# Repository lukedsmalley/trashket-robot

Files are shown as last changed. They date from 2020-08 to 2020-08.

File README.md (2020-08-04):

<div align="center">
  <h1>Trashket Robot</h1>
  <h3>Trash-catching mobile wastebasket</h3>
  <h4>Term project for GSU's Embedded Systems course in the spring of 2020 by Luke Smalley, Byron Mouen, and Christian Moronta</h4>
</div>
  
The course instructor was [Doctor Michael Weeks](https://hallertau.cs.gsu.edu/~mweeks/index.html), who maintains [this webpage](https://hallertau.cs.gsu.edu/~mweeks/csc4110/) for the course in current and past terms (Those links are active as this document is written, but is apparently running on some box inside the GSU CS department, so may not be available forever).

The statement submitted for the project abstract/goal was the following:
> Trashketball is the game that every ambitious person with a wad of trash will probably engage in. One plays trashketball using a wad of trash and a trash basket (trashket). A game of trashket ball consists of one or more attempts to toss one's trash into the basket from any distance. One wins at trashketball by throwing the trash such that it lands inside the trashket.
The goal of this project is to create a trashket that moves by itself so that it will catch any trash thrown at it with as much success as possible. To accomplish this, we must construct a mobile robotic system with the capability to track thrown objects. This requires a wastebasket be assembled with a number of other distinct subsystems:<br>- A mobility subsystem that can change direction and move quickly<br>- A vision subsystem to track thrown trash<br>- A subsystem to detect caught trash and keep score (optionally)

Prior art research yielded only the mobile trash can developed by Japanese engineer Minoru Kurata (See Kurata's [development and home demo video](https://www.youtube.com/watch?v=NqDTE6dHpJw) and [expo demo](https://www.youtube.com/watch?v=ZNWd4FFYDv0)). Kurata's trash can uses an elaborate custom-fabricated driving base that allows it to change its direction of travel without rotating the chassis or wastebasket. Thrown trash was tracked using a wall-mounted Microsoft Kinect. Duplicating the mobility system of this device was well beyond our fabrication capabilities. Based on this research, we knew we could either approach object tracking using a stationary camera or a camera mounted to the mobile assembly.

### Initial Prototype

We had plenty of hobby microcontrollers and cameras available between ourselves, but no suitable sets of compatible chassis parts and motors. Since suitably-powerful motors are expensive in the context of a college course, we designed the driving base using the minimum number of motors necessary. A two-wheel, two-motor driving base would minimize the cost of parts, albeit sacrificing our ability to turn quickly. We prepared to buy the lowest-cost motors, but a friend lent us a pair of [VEX 393 motors](https://www.vexrobotics.com/motors.html), along with the 7.2V batteries used by the VEX system.

LEGO Technic parts were the most readily accessible material for a chassis, but the VEX motors needed to be attached to the LEGO beams, gearing, and wheels. Because we had access to a 3D printer, we designed and printed components to connect VEX motors and axle to Technic parts.

<div align="center">
  <p><i>Renders of the VEX-LEGO axle coupler and motor mount bracket</i></p>
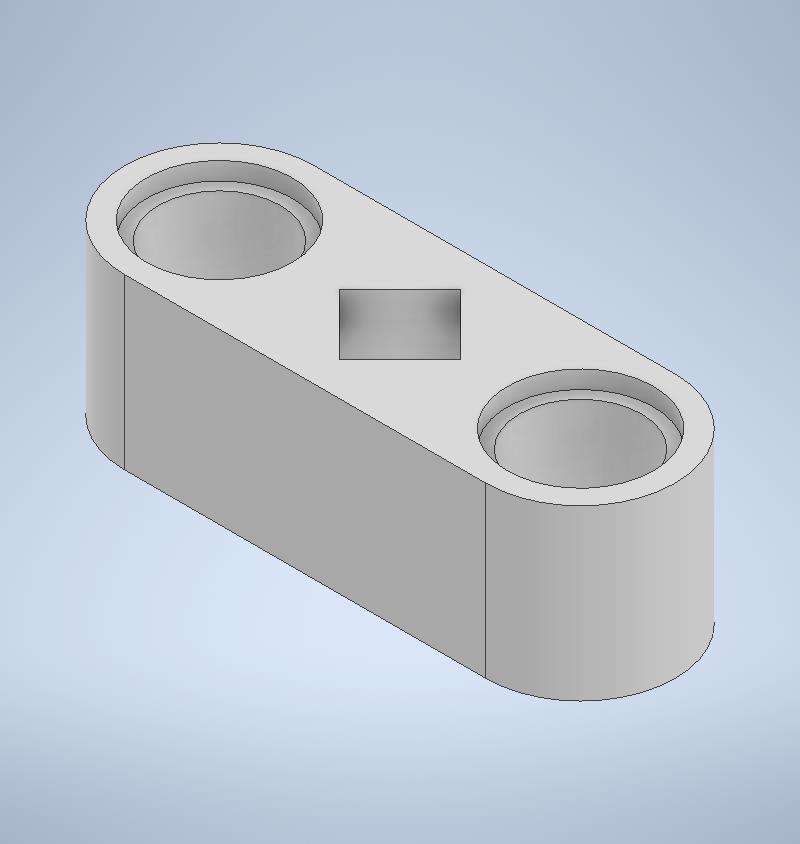
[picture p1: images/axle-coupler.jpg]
Render of the VEX-LEGO axle coupler
  
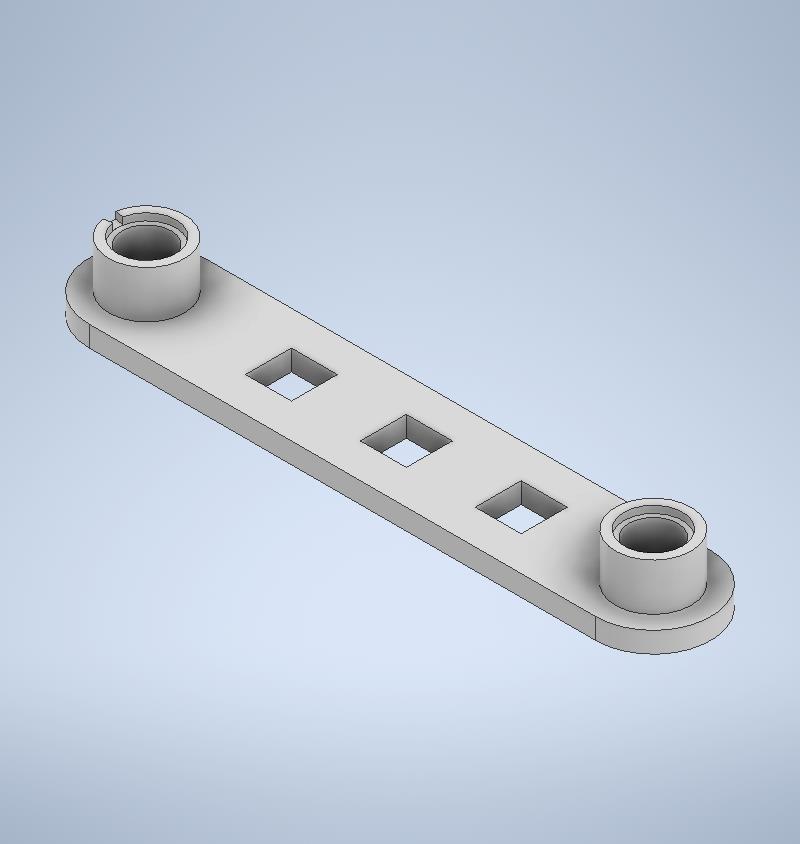
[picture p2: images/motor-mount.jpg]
Render of the VEX-LEGO motor-mounting bracket
  
  <p><i>VEX motors with 1/8" axle mounted and interfaced with the final LEGO chassis</i></p>
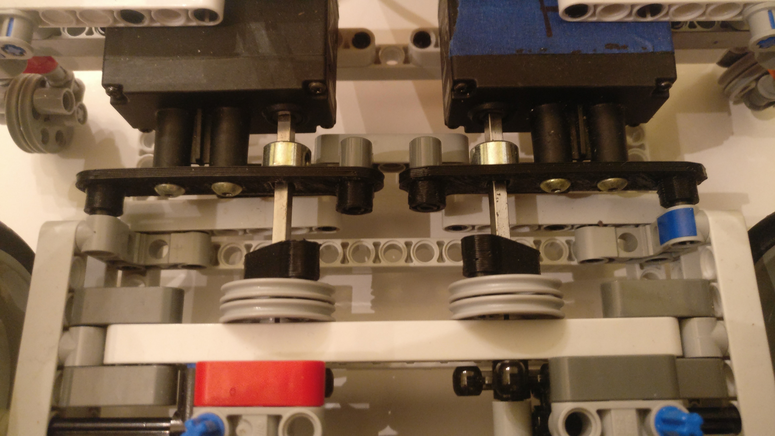
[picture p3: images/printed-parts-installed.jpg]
Photo of the VEX motors mounted tot he LEGO chassis
  
</div>

An initial prototype served as proof-of-concept for the circuitry, though it was not complex. The chassis was constructed to carry the minimum necessary electronics, but not a full-sized trash can. This first assembly was also a test of strength for the chassis and gearing, to see if the LEGO parts could support the torque of the VEX motors. The prototype only used two MOSFETs to control the motors, and could only drive forward. The electronics configuration of the first prototype was as follows:

```
    +--------------+                 +--------+     +------------+
    | 7.2V Battery | -----------.--> | MOSFET | --> | Left Motor |
    +--------------+            |    +--------+     +------------+
           |                    v         ^ 
           v                 +--------+   |    +-------------+
+-----------------------+    | MOSFET | --:--> | Right Motor |
| 6-12V to 5V Converter |    +--------+   |    +-------------+
+-----------------------+         ^       |
           |                      |       |
           v                      |       |
   +-----------------+            |       |
   | Raspberry Pi 3B | -----------'-------' 
   +-----------------+
```

<div align="center">
  <p><i>Wonderful photo of the first prototype</i></p>
  Photo of the first prototype
</div>

A worthwhile note about the photo above: the black PCBs slotted into the breadboard are the MOSFETs which regulate motor speed. The boards include a transistor and opto-isolator between the control pin and MOSFET base. Unnecessary as that may be, I already had several around. Additionally, I'm not an electrical engineer.

We used a very simple Python program, running on the Raspberry Pi depicted above, to verify that the robot functioned:

```python
# trashket-robot/scripts/circle.py

from gpiozero import PWMLED
from time import sleep

left = PWMLED(17)
right = PWMLED(22)

try:
  left.value = 0.1
  while True:
    right.value = 0.1
    sleep(2)
    right.value = 0
    sleep(2)
except: # Ctrl-C is used to interrupt the loop and end the program.
  left.value = 0
  right.value = 0
```

### Final Prototype

Since the first prototype functioned properly, a redesign of the chassis began. The base was rebuilt large enough to support a mounted wastebasket. Larger wheels were used to provide as much speed as possible. The increase in size meant that the complicated gear train from the first prototype could be reduced to a single 90-degree turn from each motor to its respective wheel.

<div align="center">
  <p><i>Reconstructed chassis with a larger body and larger wheels</i></p>
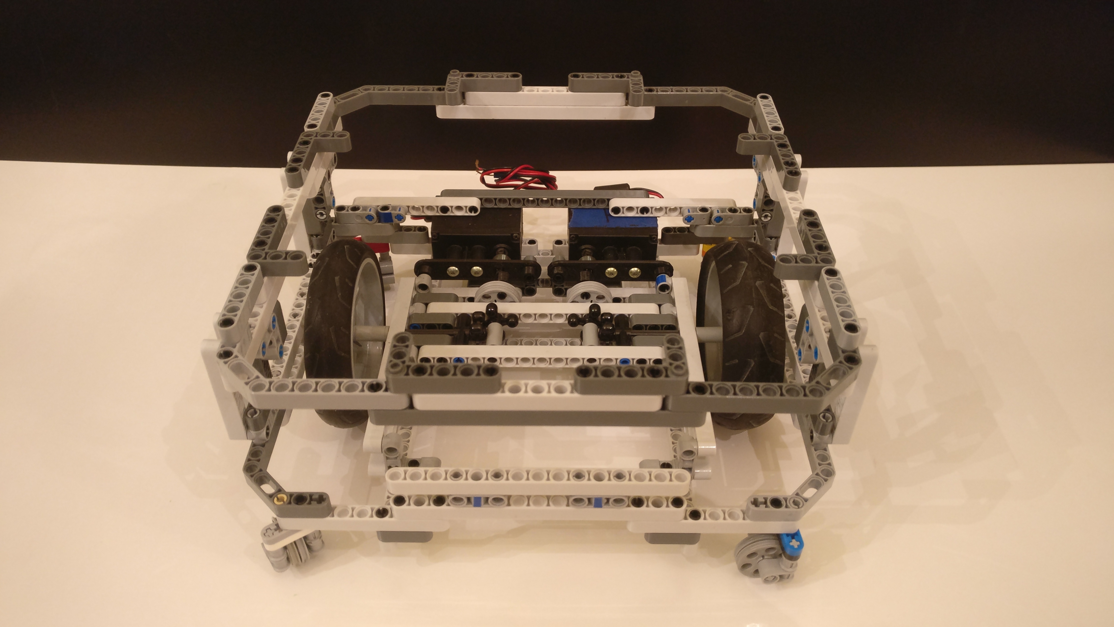
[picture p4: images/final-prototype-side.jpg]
Photo of the larger chassis and wheels
  
  <p><i>The reconstructed chassis with the wastebasket mounted atop</i></p>
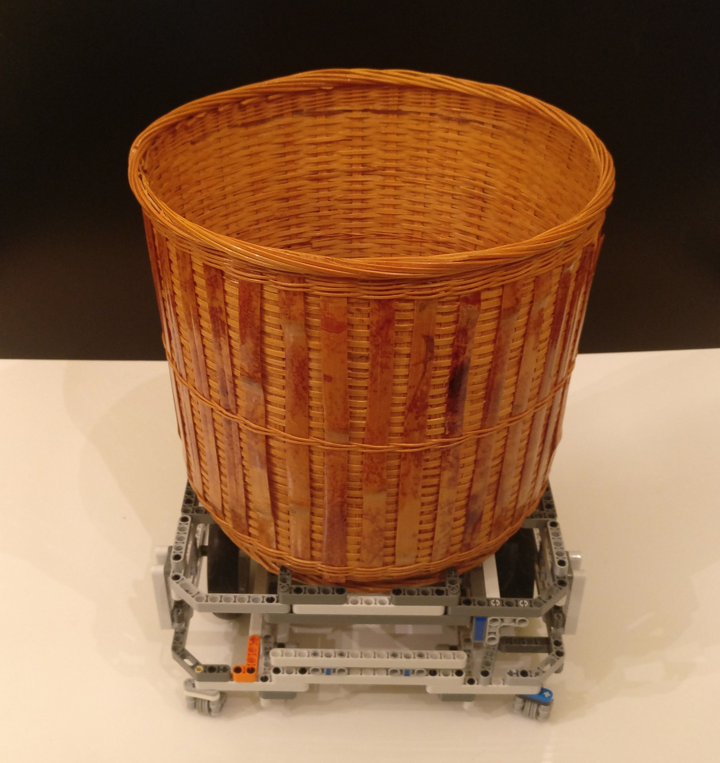
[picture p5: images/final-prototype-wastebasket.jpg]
Photo of the chassis with wastebasket atop
  
  <p><i>A top-down view of the reconstructed chassis</i></p>
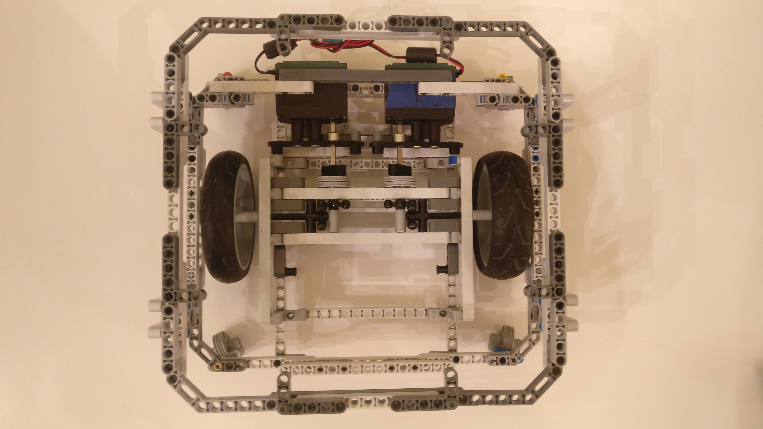
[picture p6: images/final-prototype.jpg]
Top-down view of the reconstructed chassis
  
  <p><i>An ultra-simple drive chain</i></p>
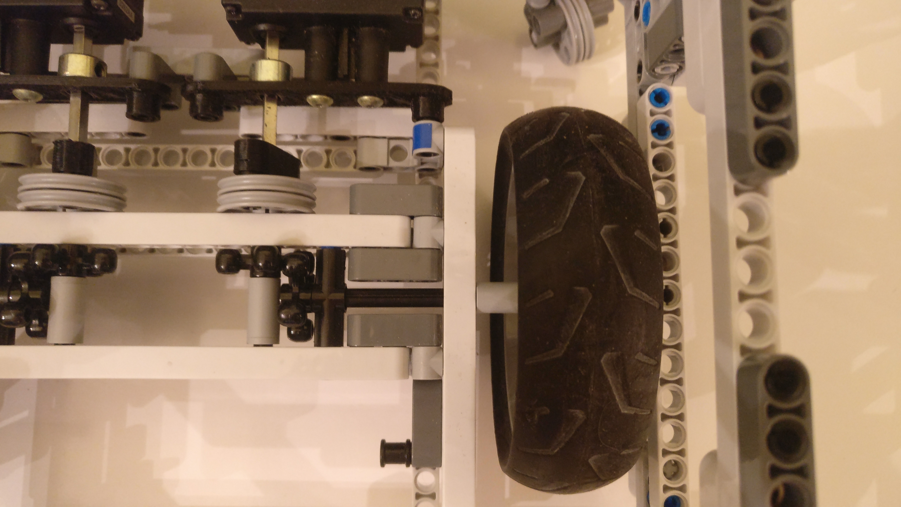
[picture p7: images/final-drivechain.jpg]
Top-down view of the reconstructed drive chain
  
</div>

The circuits for the final model underwent several changes, as initially I thought four MOSFETs could provide bi-directional control for the motors. This was because the schematics for the MOSFET boards included diodes, so I had assumed backwards current flow was not possible. Several configurations, which all produced that wonderful blue smoke, proved this not to be the case. This development occurred during our final group meeting, which was before or near the beginning of Georgia's COVID shelter-in-place recommendation. As a result, the latest and final iteration of the robot uses an 8-relay board and a single MOSFET to control driving direction and speed, respectively. This was what we had on hand at the time the final changes had to be made. We also anticipated a need to upgrade to a double-battery configuration due to lack of power, but actually the change had to be made for a separate reason. The current drop resulting from engaging the motors consistently caused the Pi to reboot, so we moved the controller to a separate battery. The final electronics were arranged as such:

```
    +--------------+      +--------------+   
    | 7.2V Battery |      | 7.2V Battery |                          +------------+
    +--------------+      +--------------+                     .--> | Left Motor |
           |                      |                            |    +------------+
           v                      v                            |
+-----------------------+    +--------+     +--------------+   |    +-------------+
| 6-12V to 5V Converter |    | MOSFET | --> | Relay Module | --'--> | Right Motor |
+-----------------------+    +--------+     +--------------+        +-------------+
           |                      ^
           v                      |
   +-----------------+            |
   | Raspberry Pi 3B | -----------'
   +-----------------+
```

<div align="center">
  <p><i>An annotated photo of the final prototype electronics</i></p>
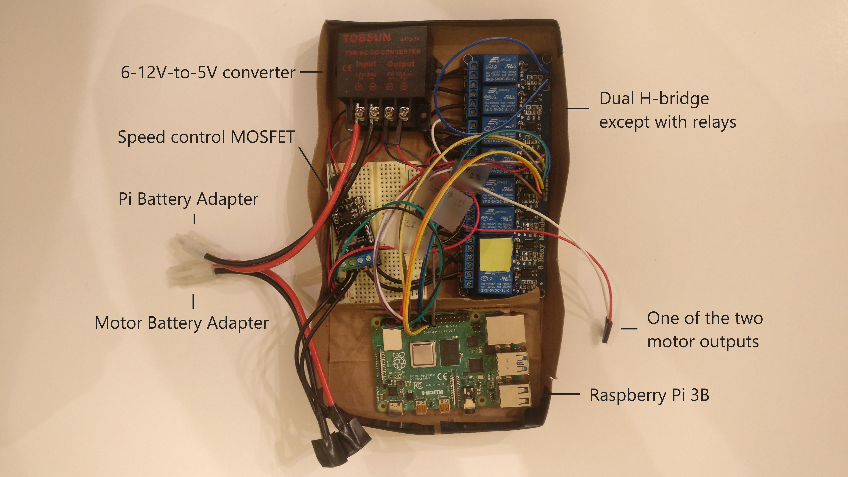
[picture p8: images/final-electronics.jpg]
Photo of the electronics used in the final prototype
  
</div>

The electronics were placed in the tray as pictured, and the tray mounts on the inside of the assembly, underneath the wastebasket, and above the batteries and drivechain. The batteries are housed in the bottom-front of the assembly.

### Premature Conclusion

We were not able to complete the project goals within the semester's time for a few reasons:
* We began devoting significant time to motion coordination via object tracking only after the driving base was fully complete.
* COVID significantly reduced our opportunities to collaborate on the project in-person.
* Issues remained in the final iteration of the driving base, but there was insufficient time to address them.

As our deadlines approached, Christian completed a script that provides remote control of the robot via webpage served from the Pi using Flask ([`scripts/server.py`](./scripts/server.py)). From that point he was also working on combining Byron's exploratory OpenCV scripts into control program ([`scripts/mask.py`](./scripts/mask.py) and [`scripts/mask_control.py`](./scripts/mask_control.py)). We mounted the Raspberry Pi camera on the front of the wastebasket, and were not forced to find change its positioning before the term ended.

Once the electronic issues were resolved in the final prototype, it became apparent that the gear-holding portions of the chassis were not constructed sturdily enough. The force of the high-torque motors and weight of the fully-assembled robot caused the beams around the gears to pull apart and allow the gears to slip. To reach a functional robot, we would have needed to reinforce this area around the gears.

The final results of the project inside the semster's time are presented in [our video](https://www.youtube.com/watch?v=Uu7vC66wiq0), which at time-of-writing is available on Christian's YouTube channel.

#### Lessons Learned
* Be diligent about dividing before conquering.
* H-bridges are four transistors, not two.
* Blue smoke smells worse than I think it does.

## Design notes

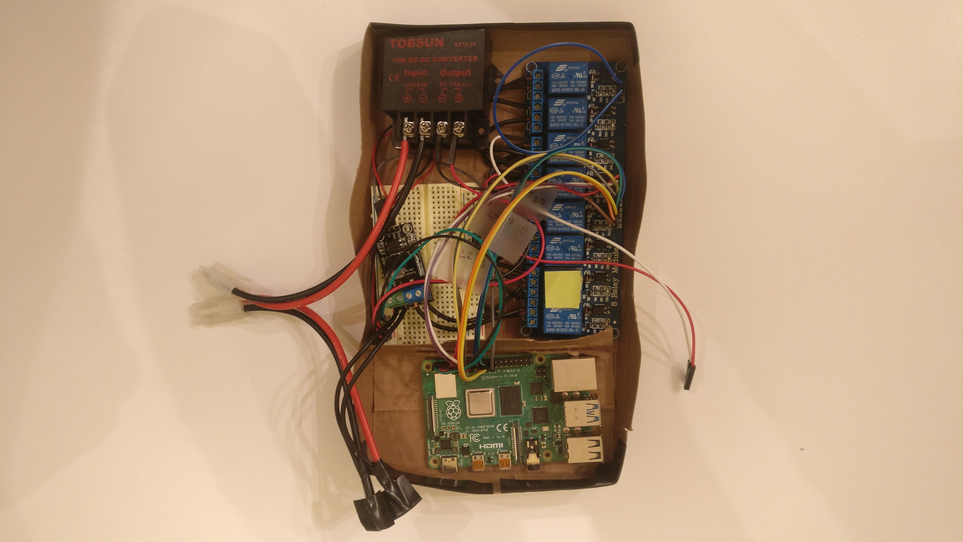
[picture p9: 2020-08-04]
images/final-electronics-unannotated.jpg

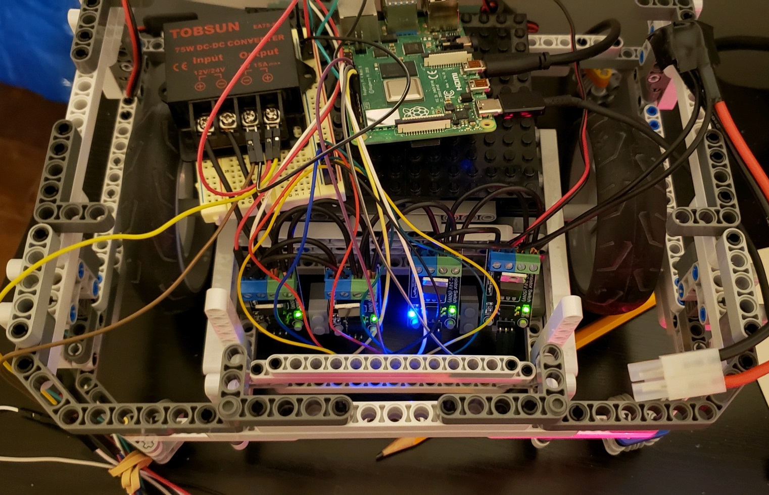
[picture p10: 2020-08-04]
images/smoke-grenade.jpg

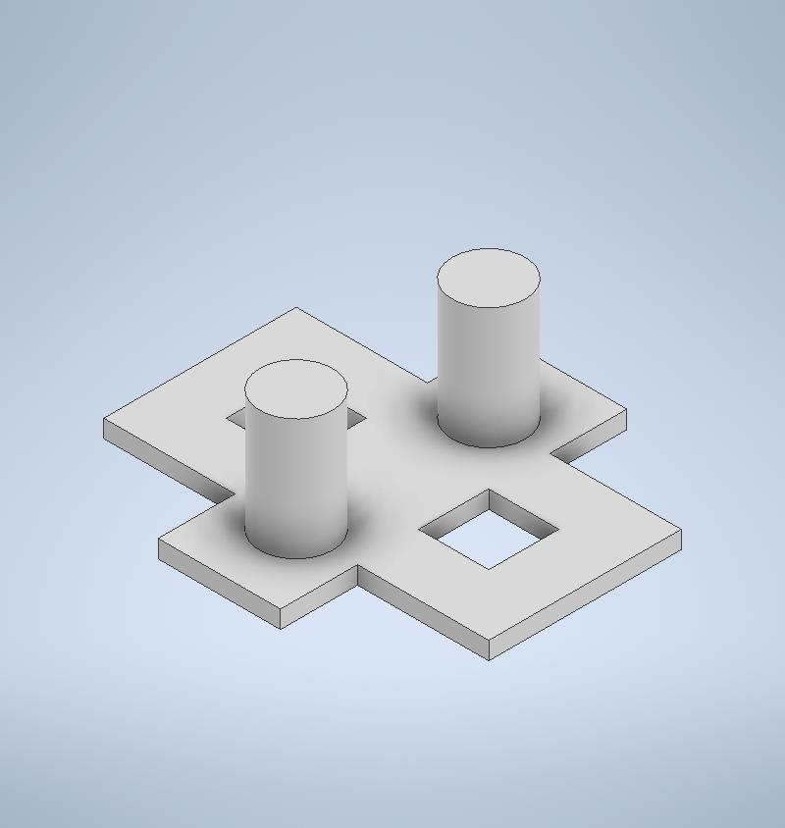
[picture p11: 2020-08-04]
models/VexLegoWidget.jpg

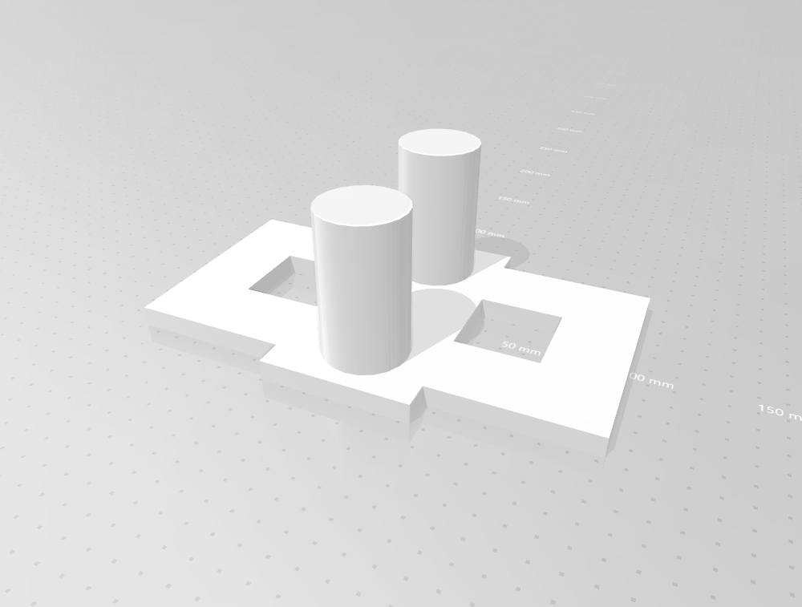
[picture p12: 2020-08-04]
models/TinkerCADWidget.PNG

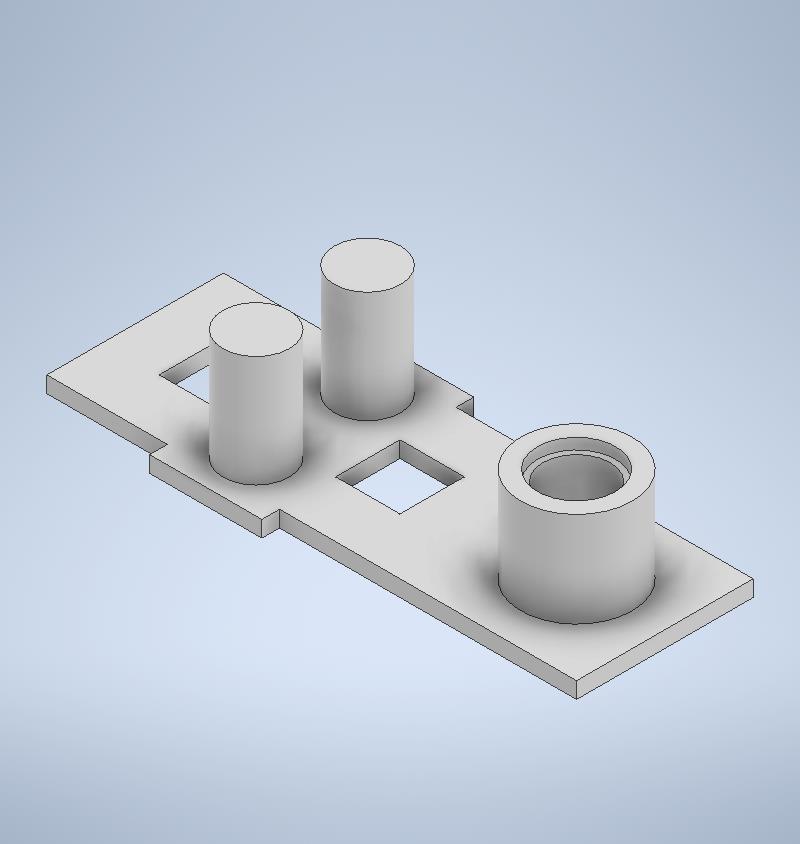
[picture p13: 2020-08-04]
models/VexLegoWidget2.jpg

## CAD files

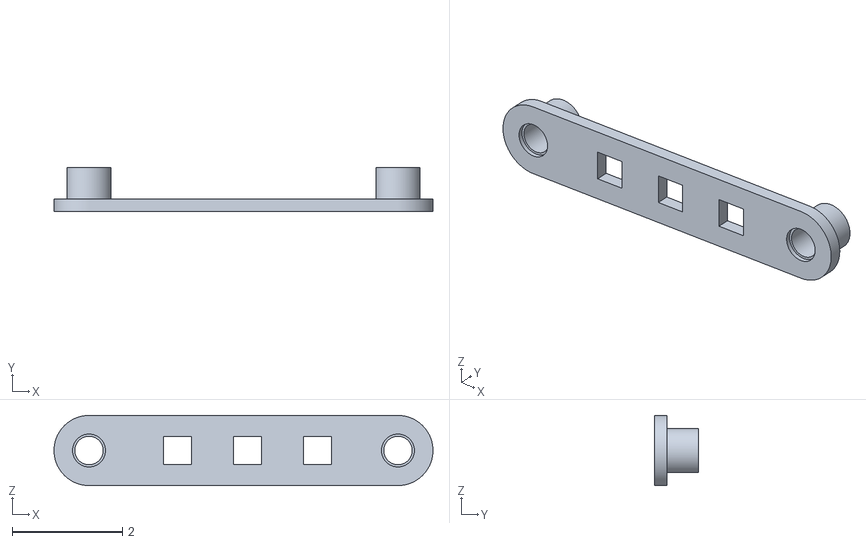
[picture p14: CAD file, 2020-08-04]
models/VexLegoMountThick.stl
6.87 x 0.8 x 1.27

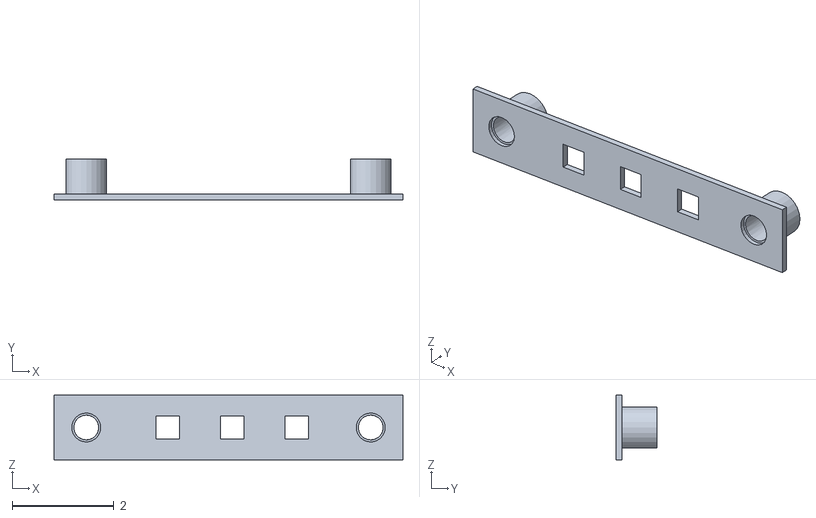
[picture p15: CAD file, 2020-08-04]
models/VexLegoMount.stl
6.87 x 0.8 x 1.27

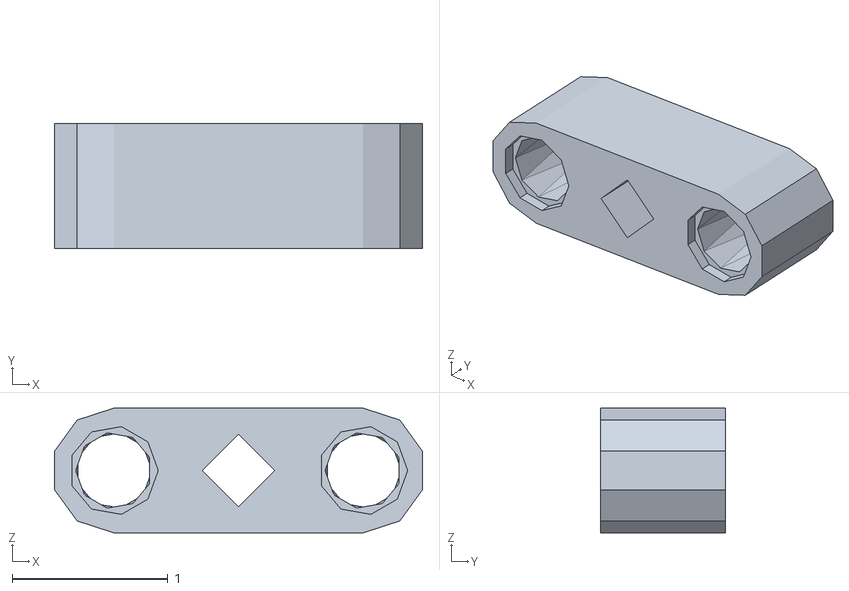
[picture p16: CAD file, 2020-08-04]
models/VexLegoCouplerBasic.stl
2.36 x 0.8 x 0.8

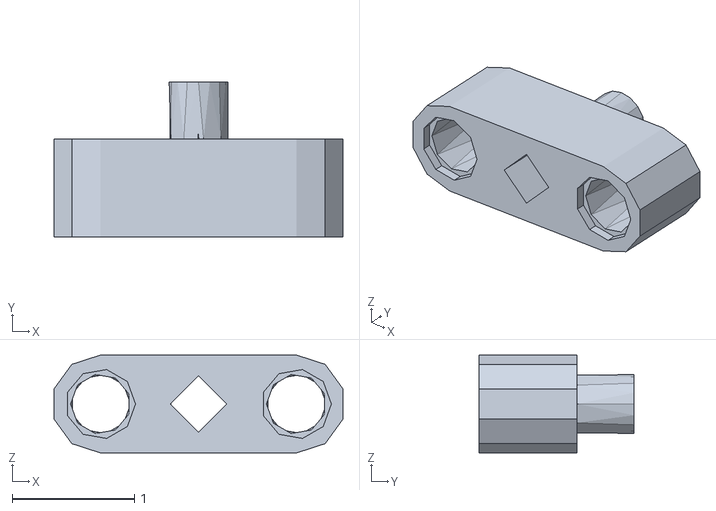
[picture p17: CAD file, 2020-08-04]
models/VexLegoCoupler.stl
2.36 x 1.26 x 0.8

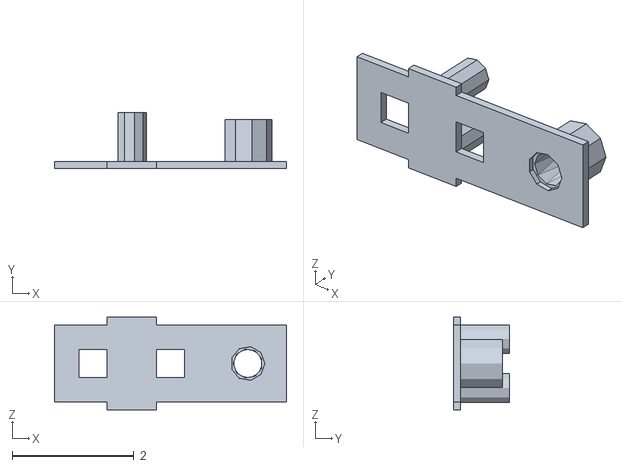
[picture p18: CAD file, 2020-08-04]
models/VexLegoWidget2.stl
3.81 x 0.917 x 1.52

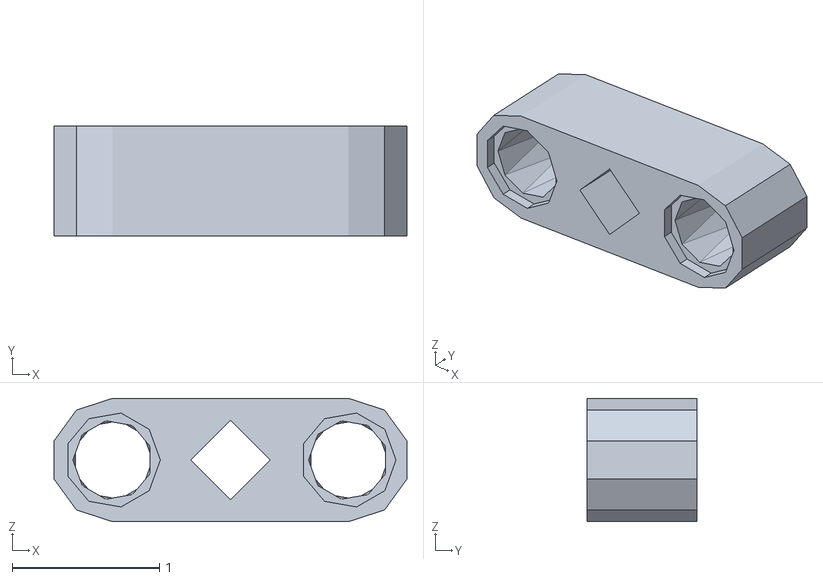
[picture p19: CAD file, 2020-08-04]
models/VexLegoBiggerCoupler.stl
2.40 x 0.749 x 0.838

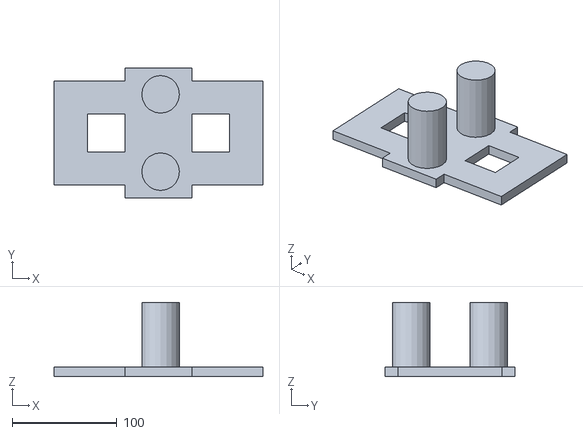
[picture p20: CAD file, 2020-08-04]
models/TinkerCADWidget.stl
200.0 x 124.0 x 71.0

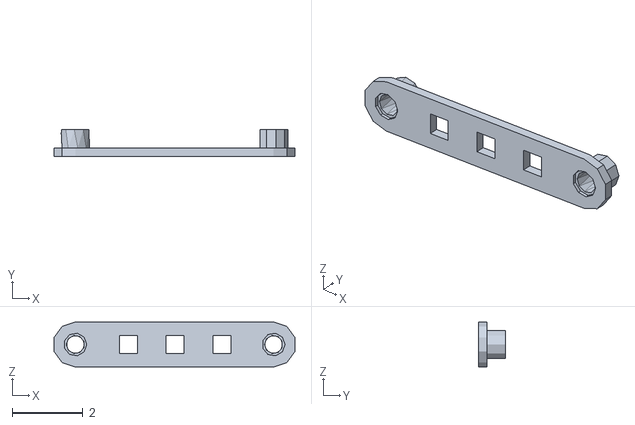
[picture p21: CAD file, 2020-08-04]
models/VexLegoMountThick2.stl
6.81 x 0.749 x 1.27

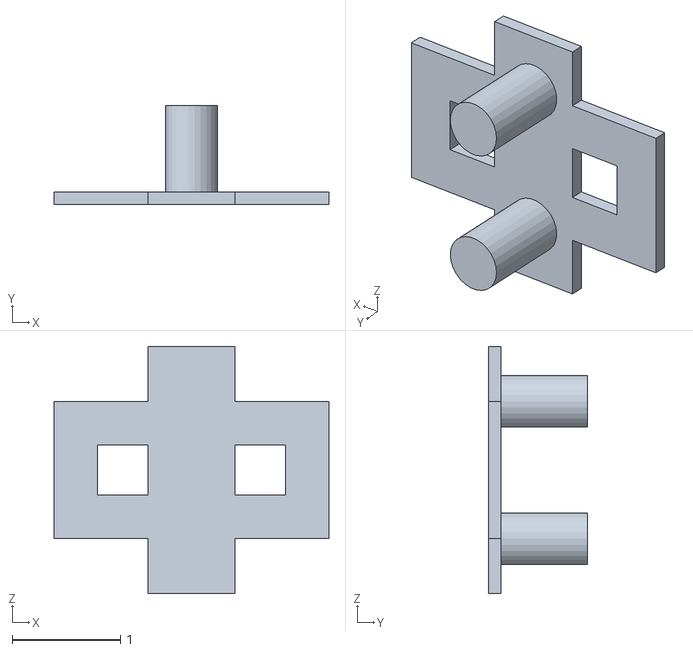
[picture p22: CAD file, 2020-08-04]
models/VexLegoWidget.stl
2.54 x 0.917 x 2.29

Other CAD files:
models/VexLegoMountThick3.stl
models/VexLegoBiggerCoupler.ipt
models/VexLegoCoupler.ipt
models/VexLegoCouplerBasic.ipt
models/VexLegoMount.ipt
models/VexLegoMountThick.ipt
models/VexLegoMountThick2.ipt
models/VexLegoMountThick3.ipt
models/VexLegoWidget.ipt
models/VexLegoWidget2.ipt

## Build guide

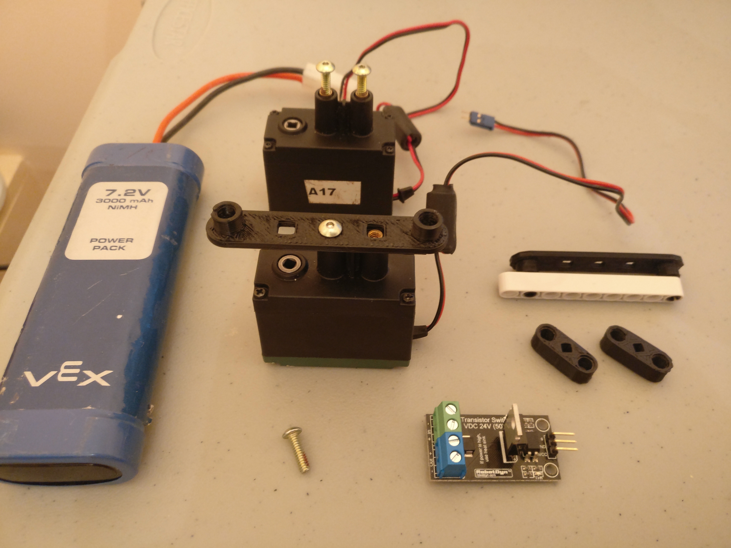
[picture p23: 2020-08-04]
images/printed-components.jpg

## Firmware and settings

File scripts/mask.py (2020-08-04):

#!/usr/bin/python
# coding: utf-8

import cv2 
import time
import numpy as np
import RPi.GPIO as gpio



# Minimum area to detect
minArea = 40


cv2.namedWindow("Normal")
cv2.namedWindow("HSV")
cv2.namedWindow("Mask")
cv2.namedWindow("Erode")


cap = cv2.VideoCapture(0)

width = 320
height = 240

if cap.isOpened():
  cap.set(3, width)
  cap.set(4, height)

  
while True:
    ret, frame = cap.read()
    hsv = cv2.cvtColor(frame, cv2.COLOR_BGR2HSV)
    mask = cv2.inRange(hsv,(90,50,20),(123,255,255))
    erode = cv2.erode(mask, None, iterations = 3)
    moments = cv2.moments(erode,True)
    if moments['m00'] >= minArea:
       x = moments['m10'] / moments['m00']
       y = moments['m01'] / moments['m00']
       print(x, ", ", y)
       cv2.circle(frame, (int(x), int(y)), 5, (0, 255,0), -1)

    cv2.imshow("Normal",frame)
    cv2.imshow("HSV", hsv)
    cv2.imshow("Mask", mask)
    cv2.imshow("Erode", erode)


    
	
	
    if cv2.waitKey(10) == 27:
        break
cv.destroyAllWindows()

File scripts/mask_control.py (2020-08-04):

#!/usr/bin/python
# coding: utf-8

import cv2 
import time
from gpiozero import PWMLED, LED

lb1 = LED(17, initial_value=True)
lb2 = LED(27, initial_value=True)
lf1 = LED(22, initial_value=True)
lf2 = LED(23, initial_value=True)
rf1 = LED(9, initial_value=True)
rf2 = LED(10, initial_value=True)
rb1 = LED(24, initial_value=True)
rb2 = LED(25, initial_value=True)

speed = PWMLED(11)
speed.value = 0.16

def forward():
  lf1.off()
  rf1.off()
  rf2.off()
  lf2.off()

def backward():
  lb1.off()
  lb2.off()
  rb1.off()
  rb2.off()

def left():
  rf1.off()
  rf2.off()

def right():
  lf1.off()
  lf2.off()

def stop():
  lf1.on()
  lf2.on()
  rf1.on()
  rf2.on()
  lb1.on()
  lb2.on()
  rb1.on()
  rb2.on()
  
def zArea(area):
  if (area<=120):
    forward()
  elif (area>=600):
    backward()
  else:
    stop()

# Minimum area to detect
minArea = 60
cap = cv2.VideoCapture(0)

width = 160
height = 120

if cap.isOpened():
  print("test")
  cap.set(3, width)
  cap.set(4, height)

while True:
    ret, frame = cap.read()
    hsv = cv2.cvtColor(frame, cv2.COLOR_BGR2HSV)
    mask = cv2.inRange(hsv,(90,50,20),(123,255,255))
    erode = cv2.erode(mask, None, iterations = 3)
    moments = cv2.moments(erode,True)
    print(moments)
    if moments['m00'] >= minArea:
       print(moments['m00'])
       zArea(moments['m00'])
    else:
       stop()
    #cv2.imshow("Normal",frame)
    #cv2.imshow("HSV", hsv)
    #cv2.imshow("Mask", mask)
    #cv2.imshow("Erode", erode)

    if cv2.waitKey(10) == 27:
        break
cv.destroyAllWindows()
